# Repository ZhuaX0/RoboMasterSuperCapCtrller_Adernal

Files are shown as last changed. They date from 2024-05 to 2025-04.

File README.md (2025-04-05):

# <center>NOMAD的超级电容模组开源

项目负责人：
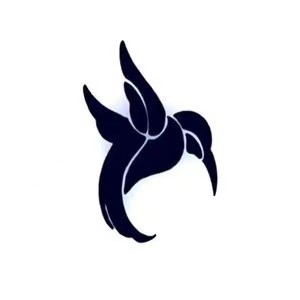
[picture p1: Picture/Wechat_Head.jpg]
Wechat_Head

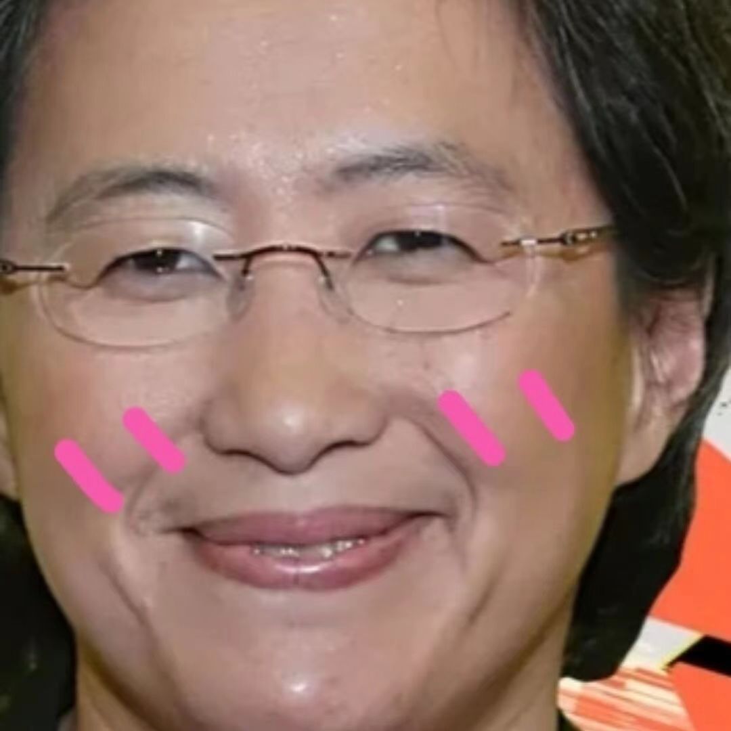
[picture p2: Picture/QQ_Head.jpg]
QQ_Head

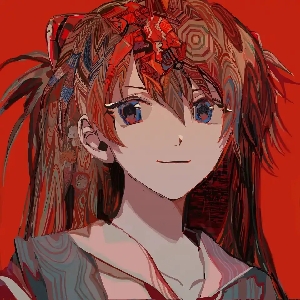
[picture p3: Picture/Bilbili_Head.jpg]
Bilbili_Head

(没错都是我)

## <center>前言
本开源文档于2024.5.5开始撰写，提笔于此，感慨万千。笔者于大一上学期入队，自大一暑假接手超电研发任务，至落笔此开源文档已有三个年头。这四年见证了队伍从联盟赛队伍一跃成为超级对抗赛的常驻队伍，笔者的技术、心态也逐渐成熟。依旧记得22赛季的赛场上，训练赛与小组赛受到单方面的薄纱而导致0胜绩大败而归，彼时的沮丧与不甘；依旧记得23赛季联盟赛，小组赛与某一线强队打平，万年弱队的滤镜被打破，彼时的兴奋与激动；依旧记得23赛季对抗赛，小组赛遇上两支国赛4强，对其实力与技术水平的由衷佩服。

笔者自接手超电研发任务以来，研发工作横跨22、23、24三个赛季。22赛季笔者技术水平不足，对队伍无实际贡献，因此22赛季的超电系购买淘宝某某创新的超级电容控制器与超级电容组使用；23赛季笔者借鉴中南大学FYT战队于CSDN的开源，研制一套可切换功率路径的串联降压方案，将其应用于赛场，并进行并联式双向四开关方案的预研；24赛季笔者对于并联式双向四开关的研制工作已经结束，并计划将其投入赛场。

本开源内容即笔者研制的并联式双向四开关方案的具体实现。纯属处于笔者的喜好，喜欢对自己的每个有代表意义的作品命名，该项目的超级电容控制器被命名为“Adernal”。**本开源项目不属于战队开源，属于个人开源**。本开源作为笔者的首次开源，将受到持续不定时的维护。由于笔者技术水平与精力有限，文档内的表述难免出现不恰当或者错误的表述(赛博口糊与赛博嘴瓢)，望各位谅解并欢迎指出。

## <center>控制器硬件设计
**该项目的物料选型请以BOM表为准，原理图中的物料仅供参考（仅仅封装与BOM表内物料是一样的）。**  
完整的硬件设计请参考PCB项目工程文件，本文档仅对项目中的关键硬件设计进行解释。
### 方案选择
笔者的研发工作进行过程中，RoboMaster高校系列赛的赛场上的超级电容控制器方案已近成熟。高校战队自行研制的超级电容控制器的硬件方案大致可划分为以下三种：

- 串联式降压/升压方案

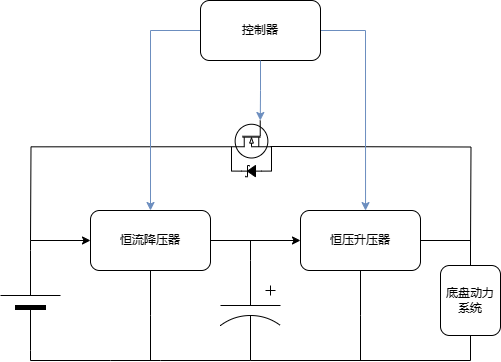
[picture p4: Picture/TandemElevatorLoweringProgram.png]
TandemElevatorLoweringProgram


该方案被认为是出现在RoboMaster高校系列赛赛场上最古早的硬件方案。来源于裁判系统电源管理模块Chassis电源接口的电流经过恒流降压部分为超级电容组恒功率（等于裁判系统功率限制）充电。电容组（可能有恒流降压输出）的能量经过一升压部分传递给底盘动力系统。此外，存在一电子开关将裁判系统Chassis电源与底盘动力系统直接连接，当电容组电压足够低导致升压部分无法正常工作时将升压部分失能同时导通电子开关。

笔者认为该方案的优点为搭建难度低，可通过选购适合的淘宝成品模块即可搭建一个可实现基本功能的硬件平台；控制难度低，控制器仅需控制恒流降压部分的使能与充电电流、升压部分的使能、电子开关的使能即可实现基本功能。该方案的缺点为硬件平台的体积过大，即便将所有硬件功能部分集成于单板、叠板，其体积对于结构组而言也是难以接受的；此外，在电容组电压较低的工况下，由于恒流降压部分与升压部分其输入、输出两端的压差较大，因此导致两者效率降低，从而导致该方案整体的能量转化效率较低，该方案在早期的RoboMaster高校系列赛受到普遍使用的原因为当时电容组的最高能量不受限制。

- 并联式四开关方案

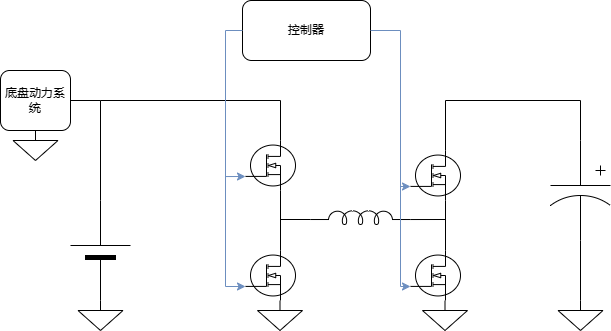
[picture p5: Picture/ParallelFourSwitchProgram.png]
ParallelFourSwitchProgram


该方案被普遍认为是当前RoboMaster高校系列赛赛场上的“版本答案”。将裁判系统Chassis电源串联一个ORing（这是可以省去的）后与底盘动力系统连接，将FSBB（Four-Switch-BuckBoost）与底盘动力系统所处网络并联，并将FSBB另一端与超级电容组连接。当底盘动力系统消耗功率低于裁判系统限制，FSBB将为超级电容组恒功率充电以保证裁判系统Chassis电源的输出功率与裁判系统功率限制保持一致；当底盘动力系统消耗功率高于裁判系统限制，FSBB将通过超级电容组的恒功率放电以保证裁判系统Chassis电源的输出功率与裁判系统功率限制保持一致。

笔者认为该方案的优点为：从功率、效率方面看，该方案性能足够高，是所有主流方案中最靠近规则限制下超级电容控制器理论最优性能的方案。该方案的缺点为：研发难度较高，存在微控制器编程与电子电路设计两大难点，并且在实际开发中，这两个难点具有较高的耦合，这要求研发者对电子电路设计与微控制器编程都具有一定的造诣（从另一个角度看可以算是优点，对这个方案的超电进行独立研发确实很锻炼人）。笔者当初想挑战自我，故将超级电容控制器的硬件方案定为该方案。

- 并联式两开关方案

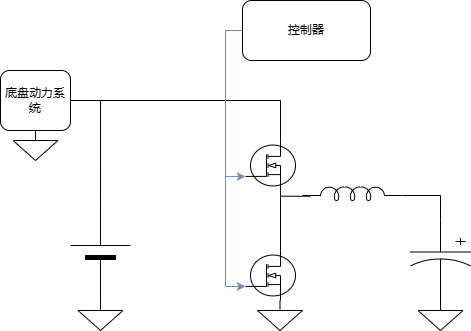
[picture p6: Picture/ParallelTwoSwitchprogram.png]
ParallelTwoSwitchprogram


该方案被认为是并联四四开关方案的简化版本。将裁判系统Chassis电源串联一个ORing（这是可以省去的）后与底盘动力系统连接，将单半桥变换器与底盘动力系统所处网络并联，并将单半桥变换器另一端与超级电容组连接。当底盘动力系统消耗功率低于裁判系统限制，单半桥变换器将为超级电容组恒功率充电以保证裁判系统Chassis电源的输出功率与裁判系统功率限制保持一致；当底盘动力系统消耗功率高于裁判系统限制，单半桥变换器将通过超级电容组的恒功率放电以保证裁判系统Chassis电源的输出功率与裁判系统功率限制保持一致。

笔者认为该方案的优点为搭建复杂度低于并联式四开关方案，相对于并联式四开关，从硬件角度看，该方案仅需要对一组半桥进行控制，从软件角度看，该方案无需考虑电容组电压处于电池电压附近时的控制问题；此外，该方案从理论上具有高于四开关的能量效率。该方案的缺点为：性能上限没有并联式四开关方案高；此外额外需要解决机器人死亡后底盘断电，电容组电压从半桥上管体二极管窜入母线导致“僵尸车”的问题。

### 关键物料选型
对于FSBB上的无源器件，笔者选型如下：

|物料类型|型号|
|:-----:|:--:|
|  C  |ZE11000UF35V119EC0014|
| L |BCIHP2213-150M|

其中，ZE11000UF35V119EC0014为容值为1000uF，20℃、100kHz下的ESR不高于8mR的高性能固态电容器；BCIHP2213-150M为感值为15uH，DCR典型值为5.62mR，额定电流为23.5A的一体成型功率电感。根据上述选型可以了解到电感纹波电流最高约为2.5A，输入/输出纹波电压最高不超过105.625mV。

对于半桥及驱动，笔者选型如下：
|物料类型|物料|
|:-----:|:--:|
|  MOS  |STL130N6F7|
|Driver |2EDF7275KXUMA1|

其中，STL130N6F7为Qg为42nC，Rds(ON)典型值为3mR的高性能N型开关管，具有不错的直流导通性能与开关性能；2EDF7275KXUMA1为灌电流8A，拉电流4A的隔离栅极驱动器，可以提供稳定的ns级的上升/下降时间。

>就目前行情来看，笔者更加推荐使用CSD18540作为开关管使用，该开关管虽然从正规渠道购买难度较大且价格高昂，但是淘宝部分商家售卖的这个管子报价为0.3RMB一颗，笔者听说该渠道的这个管子良品率高达70%(截止于2024上半年的消息)，且CSD18540的直流性能与开关性能都强于STL130N6F7。

对于模拟信号检测，笔者选型如下：

|物料类型|物料|
|:-----:|:--:|
|Sensor1|INA197AIDBVT|
|Sensor2|INA240A1DR|
|Opamp|COS722SR|
|Reference|CJ431|

其中，INA197AIDBVT为共模电压高达80V，放大倍数为50，带宽为300kHz的单向检测电流感应放大器，被放置于高侧检测母线电流；INA240A1DR为共模电压高达80V，放大倍数为20，带宽为400kHz，内置PWM抑制的双向检测电流感应放大器，被放置于高侧检测DCDC两端电流；COS722SR为供电电压在2.1V-5.5V，压摆率为7.2V/us的轨到轨运算放大器，被用来检查母线与电容组的电压；CJ431为供电电压高达36V，低至200mR的动态输出阻抗的电压基准芯片。

>当前，INA197的价格可能是绝大部分队伍难以接受的，笔者也是趁着该芯片价格低廉时购买。笔者在该项目中将该芯片作为母线功率环路反馈的提供者。考虑到裁判系统仅以10Hz反馈Chassis功率，因此母线电流的电流感应放大器可以认为仅需保证具有足够高的共模电压以满足在RM赛事工况下不会对芯片造成损坏，从这个角度来看，国内外芯片厂具有更多性价比之选。笔者不建议通过低侧采样的方式检测母线电流，考虑到RM赛事中超级电容控制器与超级电容组之间存在裁判系统超级电容管理模块，该模块与裁判系统电源管理模块之间存在着4Pin通讯线的直接连接（包含GND），不排除电流从4PIN线直接回流至裁判系统电源管理模块的可能性，导致低侧采样出现失准。

>针对于FSBB两端的电流采样，笔者认识到PWM抑制功能的用处是有限的。在INA240的数据手册-典型应用中，INA240被放置在半桥的SW网络检测无刷电机三相线的电流或螺线管的电流，但是INA240不适合放置在超级电容控制器的SW网络。下图为INA240数据手册中展示PWM抑制能力的曲线图，考察可知发生共模电压阶跃后输出反馈的失准时间约为1us，以该项目超级电容控制器为例，开关频率为160kHz，上升沿失准与下降沿失准占据整个开关周期约32%，半桥占空比较大或较小可能导致INA240无法反馈准确的电流值。(还在用INA240的原因是懒得改了)笔者在此更推荐采用低侧电流检测方案并直接使用运放搭建采样电路，可以更好的降低成本并锻炼开发人员的模拟电路搭建调试能力。
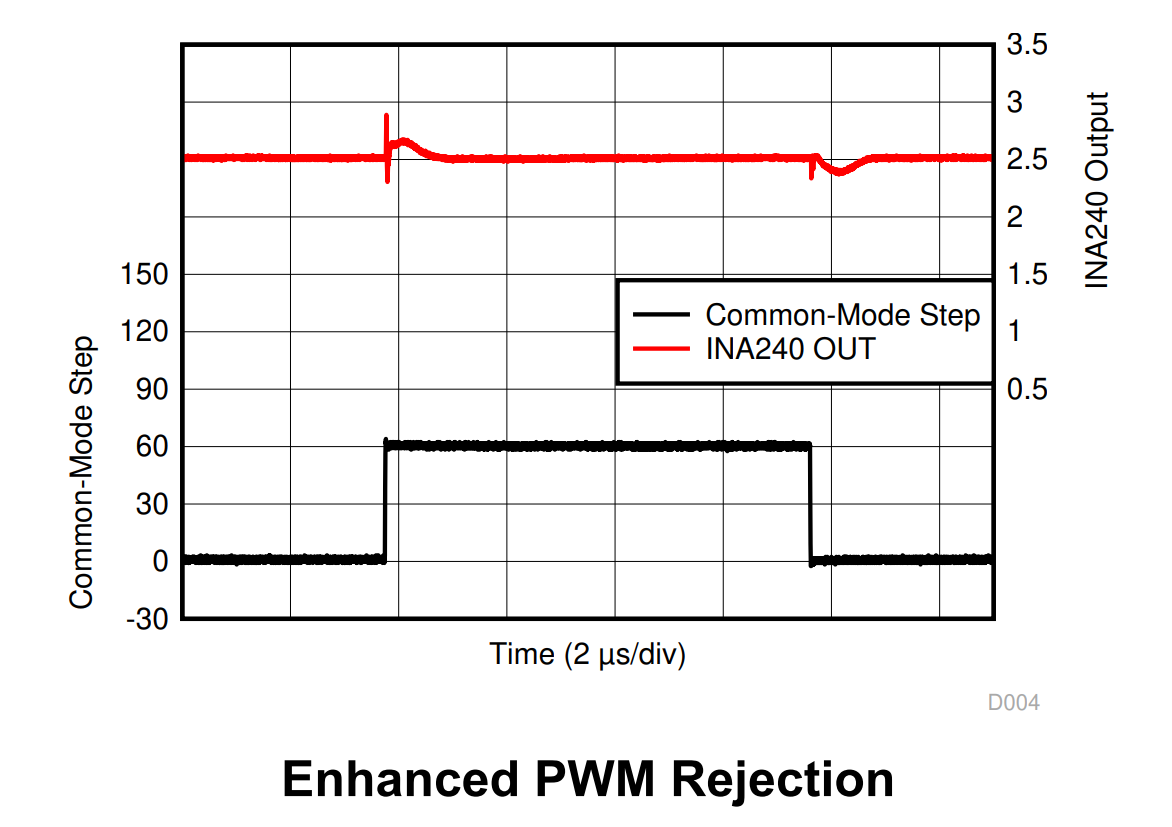
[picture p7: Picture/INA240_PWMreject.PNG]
INA240_PWMreject


在该项目中，以下杂散物料的选型也值得一谈：
|物料类型|物料|
|:-----:|:--:|
| C |CL21B473KBCNNNC|
|MicroControllerUnit|STM32G474CET6|

其中，CL21B473KBCNNNC为三星的容值47nF的MLCC，笔者在迭代过程中发现半桥SW噪声约为40-50MHz，该噪声耦合到整板的电压轨与信号网络导致超级电容控制器工作出现异常。笔者了解到该MLCC在30-70Mhz下具有30~50mR的阻抗（见下图）,在关键位置的电源轨铺设该MLCC，提高了整机工作的稳定性；STM32G474系意法半导体推出的主流微控制器，D-Power产品组合的一员，专门针对数字电源相关应用，例如D-SMPS、照明、焊接、太阳能系统逆变器及无线充电器。内置高分辨率定时器可提供高达184ps的分辨率，为电源提供精确电流、功率控制。

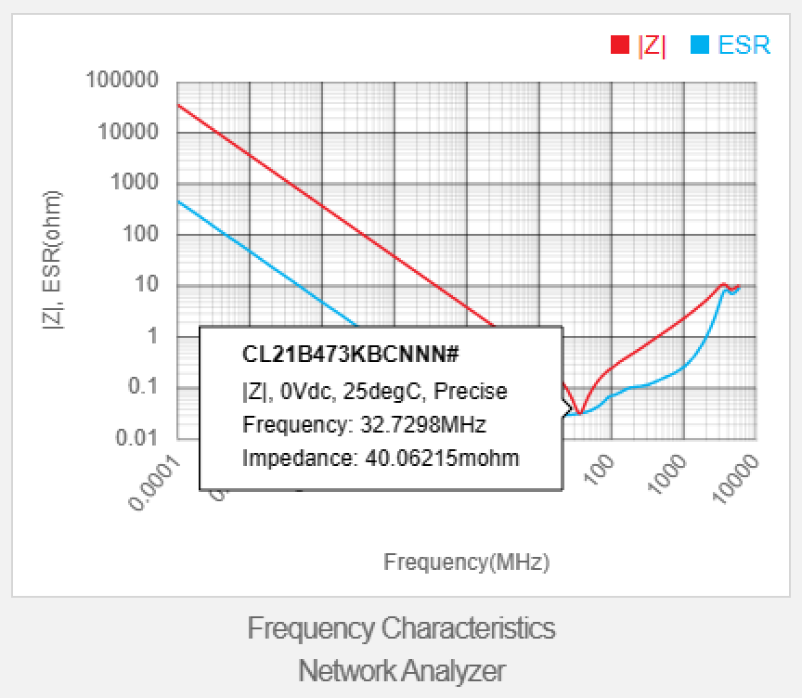
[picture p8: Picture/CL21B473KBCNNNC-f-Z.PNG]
CL21B473KBCNNNC-f-Z


### 关键电路设计
原理图中物料型号仅作为参考。

- 半桥驱动电路

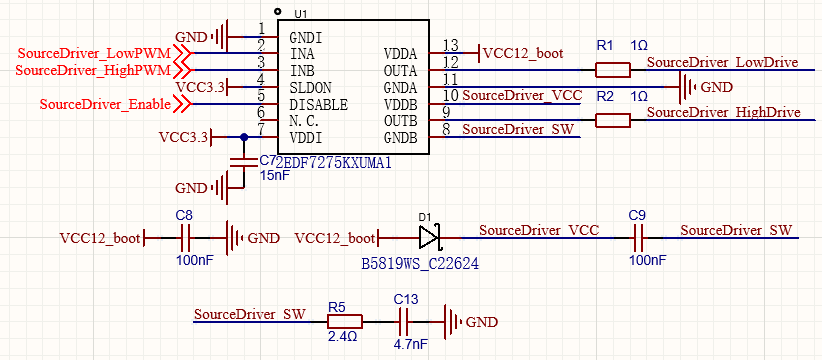
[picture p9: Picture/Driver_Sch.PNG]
Driver_Sch


对于半桥驱动器的控制部分，内置LDO未启用，电源轨直接使用数字信号的3V3电源；对于半桥驱动器的驱动部分，高侧N型开关管直接使用自举电路驱动，栅极驱动输出与开关管通过R1,R2电阻连接，用处是吸收Vgs振荡与减缓开关管的开启/关断时间以抑制电磁问题。R5、C13为RC组合，用于吸收半桥开关时SW网络的振荡能量，R、C值的敲定遵从[Analog Design Journal-Slyt740-Reducing noise on the output of a switching regulator](https://www.ti.com/lit/an/slyt740/slyt740.pdf?ts=1702068348410&ref_url=https%253A%252F%252Fwww.bing.com%252F)。
<br>
- 缓启动/防反接电路

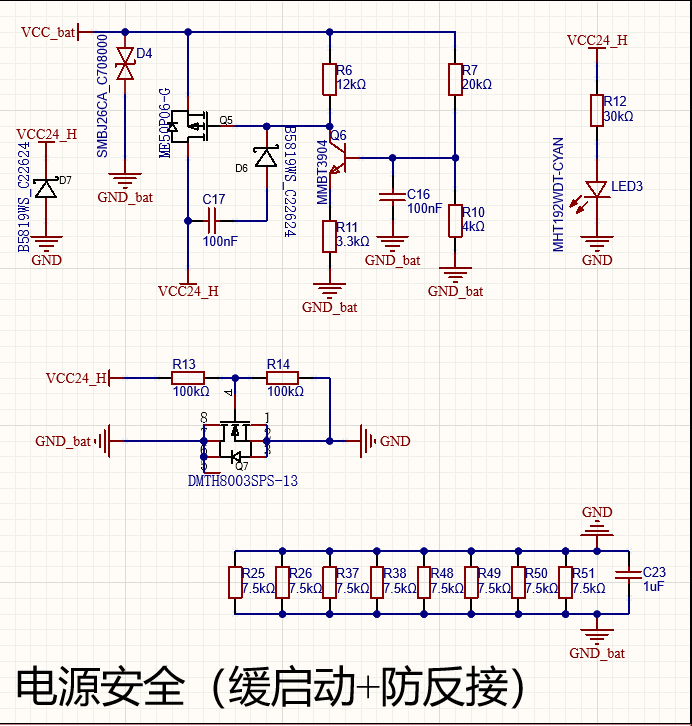
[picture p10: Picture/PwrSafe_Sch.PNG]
PwrSafe_Sch


电源硬件缓启动依托P型开关管的弥勒效应实现。当VCC_bat电压上升，VCC_bat通过R7、R10给C16充电，延长Q6(NPN-bjt)开启时间，Q6开启过程中，R6两端压差逐渐增大，Q5的Rds快速减小，当VCC24_H网络有0电压迅速上升至VCC_bat，经过C17与D6为P型开关管的栅极补充电荷，延长米勒平台。在Q5完全开启后，母线上任何电压尖峰的能量都由D4(TVS)消耗。  
防反接通过通过低侧N型开关管实现。当VCC24_H上升并保持稳定，经过R13、R14分压，Q7正常导通。当发生反接，GND_bat网络为电池电压，Vgs为0，Q7阻隔反向高压，实现防反接功能。考虑到未反接时，VCC24_H电压下降导致Q7挂断，此时GND为浮地，因此在GND与GND_bat间连接RC将GND网络下拉至GND_bat（别骂了笔者现在也觉得没啥用），反接时，电流从GND_bat经过该电阻与D7返回VCC_bat网络，板载芯片承受的负压仅为D7的正向偏置电压。
该电路提供Multisim仿真文件。
<br>
- 信号调理

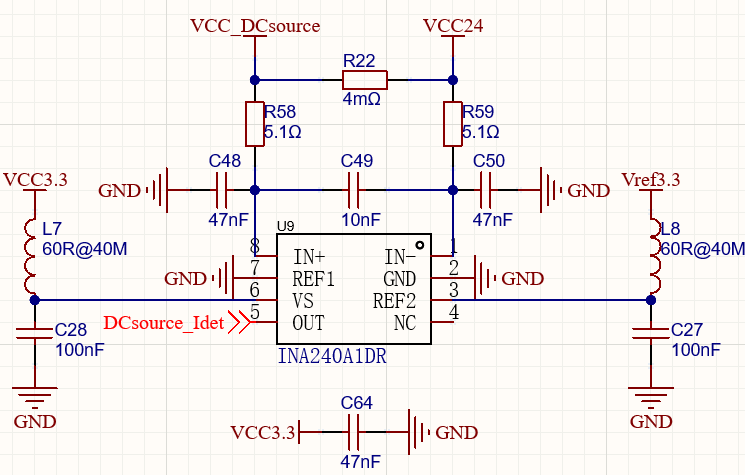
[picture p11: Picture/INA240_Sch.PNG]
INA240_Sch


以INA240的电流检测电路为例，检流电阻两端经过R58、R59、C48、C49、C50到达INA240的差分采样引脚。R58、C48与R59、C50这两个RC组合用于抑制半桥SW噪声耦合到电源轨上导致的共模瞬变，C48、C50需要连接至模拟信号参考层，C49用于差模滤波与抑制共模滤波器一致性偏差导致的差模误差。  
3V3电压基准经过L8（磁珠）与C27，经过INA240内部电阻分压为双向电流检测提供电压偏置。
>之所以为带有PWM抑制功能的INA240添加共模RC滤波器的原因在"关键物料选型"小节有所提及，下图截取与INA240的用户手册，对于5R的外部电阻，增益误差仅为0.17%，因此依旧能维持足够高水平的一致性。
>INA240_OutsideCommonModeFilter

### Layout

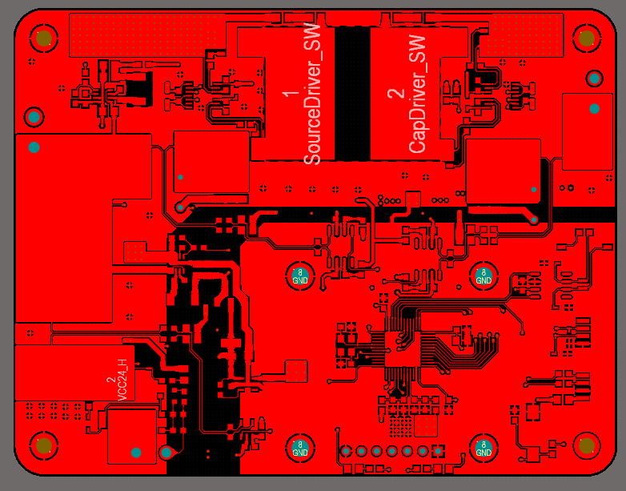
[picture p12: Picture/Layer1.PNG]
Layer1

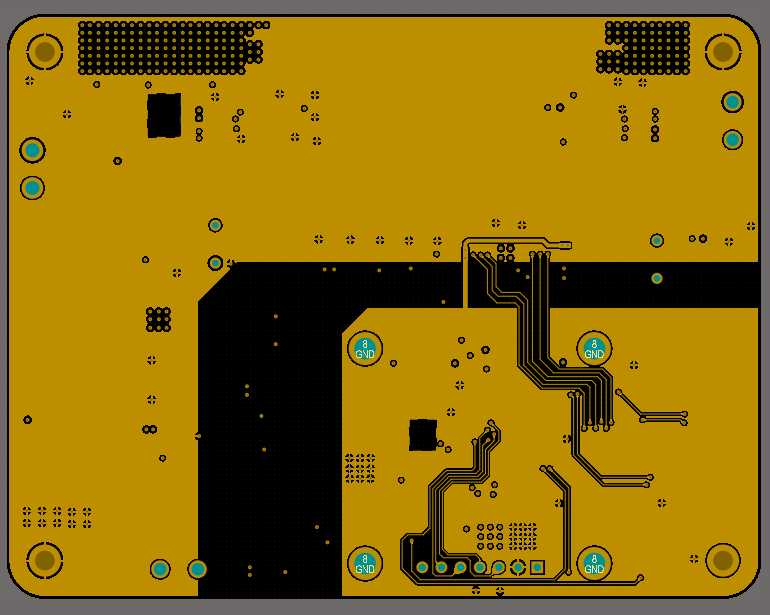
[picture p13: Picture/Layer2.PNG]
Layer2

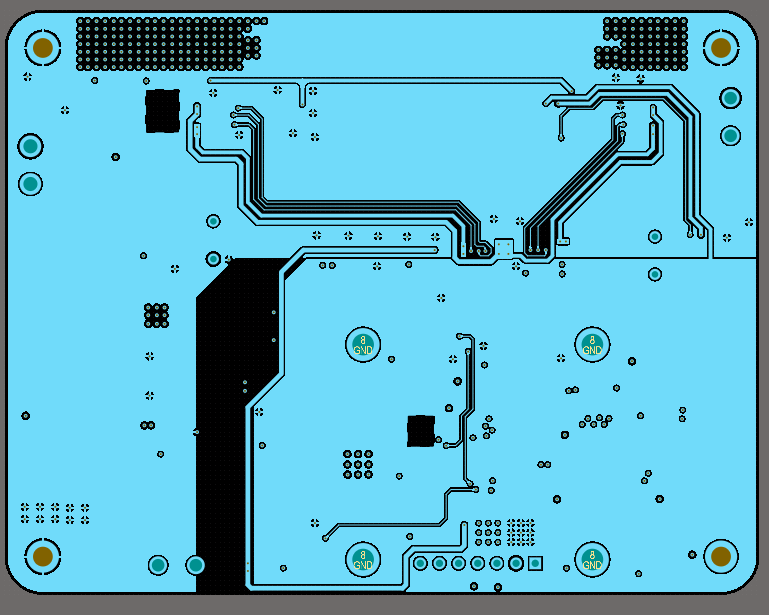
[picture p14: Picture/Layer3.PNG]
Layer3

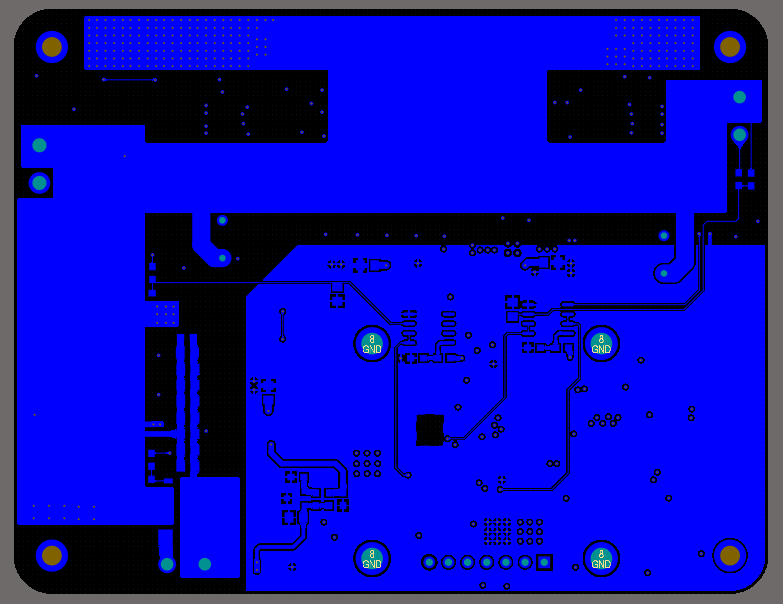
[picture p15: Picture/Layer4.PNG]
Layer4


在PCB板上，功率部分与控制部分被严格分隔，功率线通过区域填充增加宽度保证了足够的承载电流能力。功率区域中，1层铺地用于提高散热能力，2层铺地尽可能完整用以抑制杂散噪声并屏蔽其对下层信号的影响，三层铺地用于辅助散热。4层地为功率地，布置为“工字形”以保证FSBB工作过程中尽可能小的回路面积，以减小对外的电磁干扰。  
在控制区域，大部分信号器件贴装于1层，1层铺铜为数字信号参考层；2层为数字信号电源层，3层为模拟信号电源层，4层为模拟信号参考层。功率与信号的参考层通过与降压路径相同路径的走线进行单点连接，数字、模拟信号电源轨通过放置在微控制器模拟电源引脚附近的集中放置的过孔进行单点连接。

### 整体效果
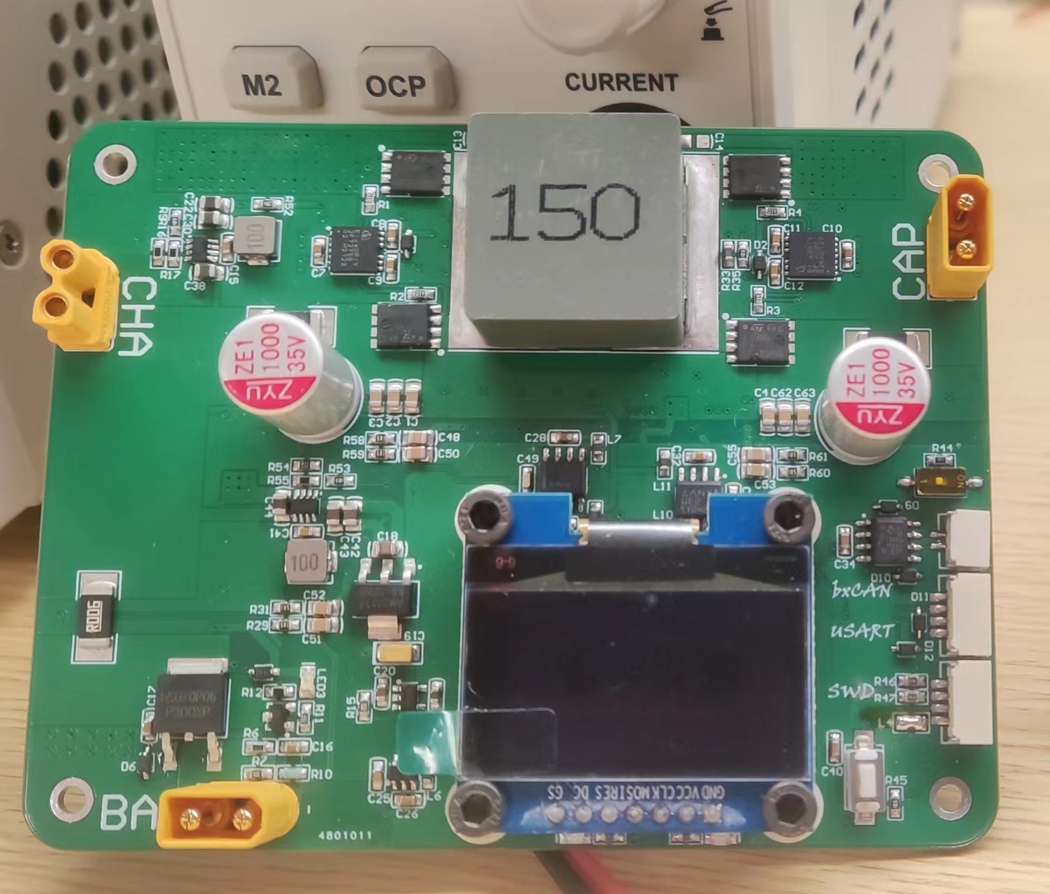
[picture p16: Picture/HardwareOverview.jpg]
HavdwareOverview


## <center>控制器软件设计
由于该项目中硬件与软件的耦合度较高，笔者对软件的开发伴随着硬件的研发工作持续了约1年的时间，不同部分的代码风格存在一定的变化。  
值得注意的是，由于控制方案的原因，本开源项目中提供的控制器软件设计并不能很好的发挥出控制器硬件的全部性能，详细的优化建议已在下文给出，根据优化建议对控制方案进行改进后，理论上将能发挥出控制器硬件的全部性能。  
STM32工程中，需要单独将LowOptZone.c与Safety.c文件的优化等级设置为-O0，以避免控制执行出现异常的现象。  
完整的硬件设计请参考STM32项目工程文件，本文档仅对项目中的关键软件设计进行解释。
### 环路控制
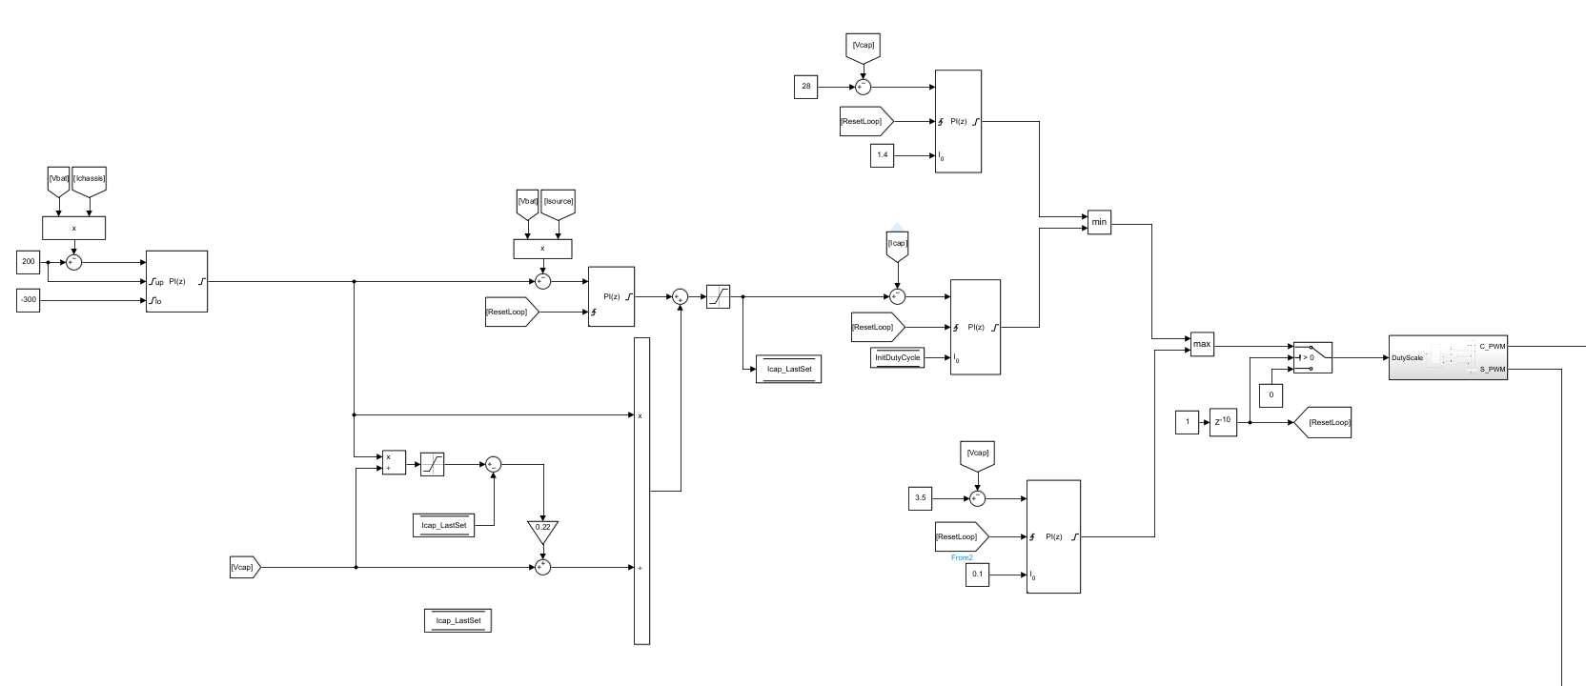
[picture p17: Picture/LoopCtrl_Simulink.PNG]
LoopCtrl_Simulink

环路控制方案的框图如上图所示。  
主环路为PID-FF-PID环路。最外层环路为母线（裁判系统Chassis电源输出）的功率PID环路，理想状态下，其期望恒定为裁判系统功率限制，反馈量为当前母线的实时功率，控制量为FSBB连接母线一端的期望功率（正负代表充电与放电）。

中间的FF环节将FSBB母线端期望功率( $P_s$ )转为电容组一端的期望电流( $I_c$ )。假定FSBB效率恒为100%（即 $P_s = P_c$ ， $P_c$ 为电容组当前充放电功率）， $I_c$ 与 $P_s$ 的关系可以通过下式直接表示：
$$I_c = \frac{P_c}{U_c} = \frac{P_s}{U_c}$$
该式被认为是简单模型，将上式引入控制环路后发现， $I_c$ 稳定后的收敛值准确，但是 $P_s$ 变化幅度较大时， $I_c$ 值出现抖动收敛的现象，其曲线类似于带阻尼的谐波曲线。  
推测上述现象是电容组的ESR导致， $P_s$ 变化后， $I_c$ 依上式发生变化，由于电容组存在ESR， $I_c$ 变化往往会导致 $U_c$ 短时间发生较大变化，因而下一次环路控制根据变化后的 $U_c$ 对 $I_c$ 进行调整。上述过程反复进行，其结果就是 $I_c$ 抖动并逐渐收敛至恒定值。解决抖动问题的方法就是将在控制模型中考虑电容组的ESR。修改简单模型为：
$$I_c = \frac{P_s}{U_c - I_{Clast}·ESR + I_c·ESR}$$
其中， $I_{Clast}$ 为上一次环路控制中FF输出的电容组电流期望值，整理得：
$$I_c = \frac{P_s}{U_c + ESR·(I_c - I_{Clast})}$$
上式被称之为ESR模型。欲求出 $I_c$ 的解析解，需要通过求根公式对二元一次方程进行求解，求出的解析解形式复杂，对微控制器运算压力较大，因此需要对上式进行简化以描述 $P_s$ 转成 $I_c$ 的过程。  
将简单模型 $I_c = \frac{P_s}{U_c}$ 引入上式中等号右边分母的 $I_c$ ，将上式简化为：
$$I_c = \frac{P_s}{U_c + ESR·(\frac{P_s}{U_c} - I_{Clast})}$$
上式被称之为简化后的ESR模型。将上式引入控制环路， $I_c$ 抖动问题得到了很好的解决，实际的 $P_s$ 可以在足够短的时间内达到预设的期望值，拥有远优于PID控制器的响应速度。但由于简化后的ESR模型不能很好的描述FSBB与电容组实际的表现，在电容组电压过低时， $P_s$ 的变化会为 $I_c$ 的曲线带来一定程度的“超调”（当然还是会收敛），在模型输入端添加数字滤波器可以很好的解决“超调”问题。理论上 $P_s$ 反馈与预设期望之间的误差与FSBB效率有很强的关联性，在本开源项目中提供的硬件平台下，若预设期望为205W，反馈值约为203W左右。

FF环节的输出作为最内环的期望值，最内环为电容组电流PID环路(正负代表电荷流动方向)，其反馈量为当前电容组的实时电流，控制量为广义占空比。

>简化后的ESR模型应用于环路控制过程中，需要对代入ESR模型的简单模型进行限幅，FF输出的电容组电流期望值也需要进行限幅，两者的限幅理应相同

>以下讨论未经实际测试（纯口嗨），请读者自行判断可行性。  
>ESR模型的表达式从形式上被认为适合使用数值迭代法得到更为精确的结果，其迭代方式类似于递归。根据ESR模型的表达式构造函数：
>$$f(x)=I_c = \frac{P_s}{U_c + ESR·(x - I_{Clast})}$$
>设定初始值 $x=\frac{P_s}{U_c}$ ，迭代一次的结果为：
>$$f(\frac{P_s}{U_c}) = \frac{P_s}{U_c + ESR·(\frac{P_s}{U_c} - I_{Clast})}$$
>上述结果与简化后的ESR模型具有相同的表达式。迭代两次的简要表达如下：
>$$f[f(\frac{P_s}{U_c})]$$
>以此类推，通过有限次的迭代，可使得计算结果与 $I_C$ 的理想期望值之间的误差小于任意的大于零的实数特定值，这种数值迭代的算法从理论上可以很好的解决电容组电压过低导致的输出失准，且不会带来部署滤波器导致时滞的问题。算法的运算时间与迭代次数近似呈正比，过多的迭代次数会对CPU带来一定程度的压力。

分析FSBB电路可以得到以下结论：
$$\frac{U_1}{U_2} = \frac{D_2}{D_1}$$
其中， $U_1$ 、 $U_2$ 分别为FSBB的1、2两端的电压值， $D_1$ 、 $D_2$ 分别为FSBB的1、2两边半桥上管PWM的duty。  
定义一 $\alpha$ 值，使其满足以下关系：
$$\alpha = \frac{U_1}{U_2} = \frac{D_2}{D_1}$$
定义FSBB的2端与母线连接（与底盘动力系统的电源轨并联），1端与电容组连接， $U_2$ 被认为是相对恒定的，因此可以得出在理想状态下 $U_1$ 与 $\alpha$ 呈正比的结论；与此同时， $\alpha$ 可以直接拆分成 $D_1$ 与 $D_2$ 。根据 $\alpha$ 的上述特性，笔者认为 $\alpha$ 很适合作为主环路的控制量， $\alpha$ 被定义为广义占空比。环路输出广义占空比后，被拆分成两边半桥的duty并更新半桥的占空比，这种控制方案被认为是解决电容组电压在电池电压附近导致存在振荡现象的有效手段。  
在实际进行的超电控制过程中，每次对FSBB提供PWM前都被建议为主环路的电容组电流环路预载积分值，预载积分值具体大小为： $\frac{U_c}{U_b}$ 。其中， $U_c$ 为当前电容组电压值， $U_b$ 为当前母线电压值，这种做法可以很好的解决FSBB于初始阶段存在短时大电流的问题。

主环路将与高电压环与低电压环竞争，高电压环与低电压环的反馈量都为电容组电压，控制量都为广义占空比。高电压环的期望为电容组的最高电压，低电压环期望为电容组的最低电压。在微控制器输出PWM前，两者都被建议预载积分值，高电压环的预载值为其积分限幅的上限，低电压环的预载值为其积分限幅的下限。

取主环路、高电压环、低电压环三者广义占空比输出的中位数，中位数对应的环路被认为竞争成功，拆分为实际占空比更新半桥duty。

>实际上，上述控制方案仍存在一定问题。若高电压环竞争成功而主环路竞争失败，主环路的所有PID环节的积分值将会持续增至积分限幅，若欲重新令主环路竞争成功，需要消耗一定的时间使积分值下降，直到主环路输出低于高电压环输出，低电压环与主环路的竞争同理，上述过程导致FSBB在特定状况下具有极慢的响应。笔者认为存在更优控制方案。需要注意的是以下对更优控制方案的讨论未经实际测试（纯口嗨），请读者自行判断可行性。
>考虑到RoboMaster高校系列赛中，裁判系统会以10Hz的频率通过串口向主控提供缓冲能量值，笔者认为可以将主环路的功率PID环替代为对缓冲能量的FF控制。定义30J为FF控制的期望值， $E_0$ 为微控制器获取到当前裁判系统反馈的缓冲能量， $E_1$ 为上一次裁判系统反馈的缓冲能量。欲保证下一次裁判系统反馈的缓冲能量为30J（维持在期望）,可以将FF控制的输出（FSBB连接母线一端的期望功率）更新为：
>$$P_s = \frac{2·E_0 - E_1 - 30J}{100ms} + P_{slast}$$
>其中， $P_{slast}$ 为上一次环路控制过程中该FF环节的输出。该式的推导不再赘述。
>笔者意识到功率环为主环路最外环的控制方案存在问题却依旧采用，原因是笔者原所处战队的历史遗留问题，战队原来很长一段时间根据缓冲能量剩余值为底盘动力系统的转矩电流乘以适当比例以实现功率控制，笔者对缓冲能量的控制在当时是不被接受的；其次，笔者对控制方案进行Simulink仿真过程中，仿真结果未出现该问题（不知道是什么原因）；最后一点是笔者没精力改了()

为了保证FSBB的效率尽可能高，对广义占空比拆分为半桥实际占空比的规则提出要求： $U_c$ 小于 $U_b$ 时，与电容组电源轨网络连接的半桥占空比为最高值； $U_c$ 大于 $U_b$ 时，与母线电源轨网络连接的半桥占空比为最高值；两边半桥上管同时开启的模态持续时间尽可能长。

环路控制方案提供Simulink仿真文件。考虑到不同版本Matlab对于打开Simulink仿真文件的一些妙妙特性，特此告知笔者通过R2022a版本的Matlab创建该".slx"文件，适配其余版本Matlab的".slx"文件恕笔者不再提供。

### 功能实现

- AlarmSystem

依托定时器上溢中断实现，同时提供多达32个非阻塞、非精确的以ms为单位的倒计时服务。该功能系项目初期实现，用于为超级电容控制器的工作任务提供时间片，对单次事件进行计时。
<br>
- Display  

更新板载OLED屏幕显示。反馈电容组电压、工作模式、安全信息等内容。
<br>
- LoopCtrl  

为FSBB提供10kHz的环路控制，FSBB的开关频率为160kHz。
<br>
- Mode  

设定三种控制FSBB的模式，分别为Silent、Work、Charge。各模式具体机制参阅《Adrenal用户手册》。FSBB的参数设定于此，最高充放电功率设定为200W，电容组一端最高充放电电流设定为13.5A。
<br>
- UsrMsg  

根据与机器人主控通过CAN帧通讯所遵守的协议，对接收到的CAN帧解包，对欲发送的信息进行封包。
<br>
- Safety  

超级电容控制器对自身的安全检查。检查项目包括8类，每类检测项根据安全事件的严重程度分为5个等级。安全管理的具体机制参阅《Adrenal用户手册》。

## <center>电容组设计

笔者认为，在RoboMaster高效系列赛的工况下，对于并联式四开关方案的控制器而言，超级电容组遵循以下以下设计规则将会得到最高的性能。

1. 超级电容组充满时，其两端电压值为30V。
2. 超级电容组充满时，其存储能量值为2kj。
3. 超级电容组的ESR需保证尽可能小。

根据以上设计规则，笔者将型号为WTR3V050F0Z-1840L的物料作为电容单体，将其按照11s1p的连接方式进行连接。  
WTR3V050F0Z-1840L为容值为50F，耐压为3V，ESR为22mR，额定电流为12A的超级电容单体。其组成的超级电容组容值为4.54F，耐压为33V，ESR为242mR。
当该超级电容组充满至30V时，其存储能量为：
$$E = \frac{1}{2}·C·U^2 = 2045.45J$$

电容组的均衡电路依托BW6103芯片实现。BW6103为是一款超级电容充电保护芯片，它内置高精度基准，确保输出精度达到±1%。内置的功率管使得过充保护后的泄流能力达到 0.2A@(VIN=2.95V)，很好地满足了超级电容级联使用时的充电特性。

考虑到200mA的泄放电流对于RoboMaster高校系列赛工况而言存在泄放能力不足的情况，考虑使用外置N型开关管AO3400A串联电阻作为主要泄放回路，BW6103此时仅用于泄放回路的触发。

提供超级电容组的PCB工程文件。

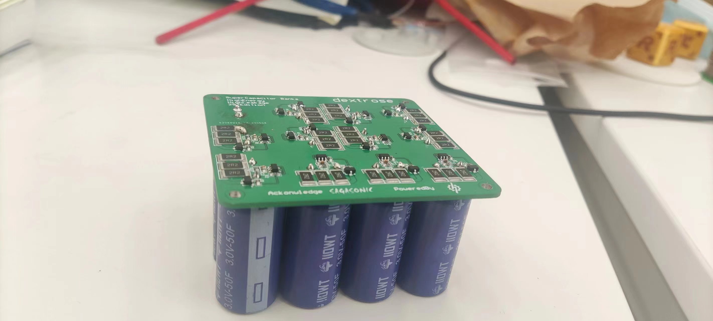
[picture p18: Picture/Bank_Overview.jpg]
Bank_Overview


## <center>实际表现

[麦轮原地陀螺](https://www.bilibili.com/video/BV1j6TweaEU2/?vd_source=5b2eb473ca9053cf0f2716bc338a787a)

## <center>后记
<!-- 感谢开源，感谢群友，感谢支持陪伴的人-->
落笔于此。笔者回想起大一入队，大二大三持续在队内干活的场景，那时候就想着，大学时光为这个比赛付出了这么多，总想留下一些什么东西不至于被忘记，故将这套超级电容控制器整理后开源。当各位看到这个文档的时候，笔者就摘下了RMer这个称号，笔者回顾自己的的RM个人生涯，倍感五味杂陈，内心再有万般不舍，也知道自己该走了，给更年轻的人腾位置，前方也有新的位置等着我。

感谢环节（不分先后）：  
感谢马斯克开源(不是  
感谢原大连理工大学凌bug战队的“光速翼”石澄今同学首次开源的《基于STM32G474的双向超级电容控制器》，笔者首次看其开源大受震撼，为笔者的开源项目的硬件方案奠定了基础。  
感谢原深圳大学RoboPilot战队的林子杰同学开源的《基于STM32F334的超级电容控制器》，其开源中的部分Layout思路解决了笔者画板时候的困惑，与其交流也收获颇丰。  
感谢西交利物浦大学GMaster战队的超级电容控制器开源，其开源中的数字滤波方案被笔者在本开源中很好的沿用。  
感谢原河北工业大学山海Mas战队的“Sirius-RX”同学，笔者时常与该同学交流超级电容控制器的研发心得，虽然其本人也独立开源研发成果且具有足够高的质量但是好像没发到RMbbs上面，因此似乎没什么人气，欢迎前去[围观](https://github.com/Sirius-RX/SP_Ultra_CAP/tree/main)。  
感谢香港科技大学ENTERPRIZE战队开源的《数控超级电容方案开源》，其开源中详细的安全处理部分很好的启发笔者。  
感谢广州城市理工学院野狼队的“空格”同学，请我吃了寿司和薯条，为我的研发工作提供能量（物理上的）。  
也感谢RM硬件交流群（826872833）的各位活跃群友，在笔者研发过程中，经常在群里问各种问题，吃百家饭。笔者有今天的技术水平与研发结果离不开各位群友的慷慨喂饭。  

## 补充

### 授权1

兹授权“深圳斯特埃科技有限责任公司”使用本开源项目用以商业目的。

授权期限：  2025  年 4 月 5 日至  2026  年 4 月 5 日。

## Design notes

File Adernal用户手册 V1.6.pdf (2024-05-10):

# Adernal 超级电容控制器用户手册

此文档为用户手册，以尽可能简洁易懂的语言让使用者快速上手而编写

## 警告！严禁将人体皮肤或任何静电源接触在任何工作状

## 态下的超级电容控制器！

## 严禁将超级电容控制器置于任何高温热源附近！

## 超级电容控制器为高发热器件，使用时注意散热。

此超级电容控制器仅为 DEMO 版本，仅在实验室条件下稳定工作，不保证其在任何条件 下皆能稳定工作，特此告知。

版本 | 主要改动 1.0 -- 1.1 修改控制帧、反馈帧内容 1.2 修改初始化帧内容 1.3 ①完善“Work 模式”的表述。 ②完善“工作强度”的表述。 ③修改协议的 Exceed 部分。 ④修复反馈帧字节数错误问题。
| ⑤对电容组插接时电压提出要求。
1.4 | ①重构对“安全管理”的表述 ②添加 OLED 屏幕显示信息的释义
1.5 | ①完善对 ”Exceed ”的表述 ②修改对“工作强度”的表述
1.6 | 为 Exceed 功能添加注意事项

# 一、 装配

超级电容控制器提供 4 个适合 2.5 直径螺丝固定整板的通孔，可以将超级电容控制 器与任意刚体固连。具体尺寸见下图（高度约为 21）。

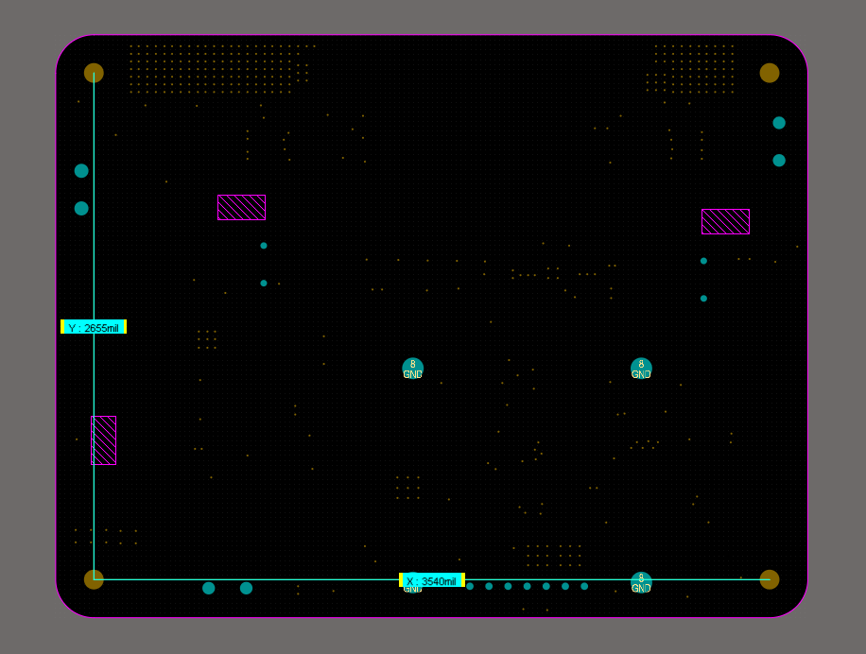
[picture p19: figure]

原则上，超级电容控制器的装配位置需要与高温热源（例如电源管理模块）及电磁 敏感装置（例如场地交互模块）保持尽可能远的距离。
若装配位置不可避免地需要靠近高温热源，需要对热源与超级电容控制器部署尽可 能完善的散热措施（包括且不限于贴装散热片、风扇主动散热），并且从软件上限制超 级电容控制器的 Pchassis 期望功率。压力测试过程中的热成像图如下： 压力测试过程中的热成像图如下：

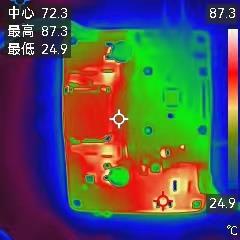
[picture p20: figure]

若装配位置不可避免的需要接近电磁敏感装置，并且在实际工况中已经对电磁敏感 装置的工作产生了一定的影响，可以要求硬件工程师在控制器上的 R5,R8 焊盘上贴装 0805 或更大尺寸的 2R4 电阻，在 C13,C14 焊盘上贴装 0805 或更大尺寸的 4.7nF 陶瓷 电容，需要注意陶瓷电容需要在 0~30V 的偏置下保持尽可能稳定的容值，这种举措可 能会导致一定程度上的板级发热。
超级电容控制器需要尽可能避免受到瞬时大冲量的冲击以免造成板载元件损坏。针 对于上述问题，一种可行的装配方案如下示意图。

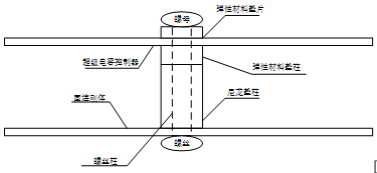
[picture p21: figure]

[图片]

上述方案中，超级电容控制器基板需要与机器人所处地面平行，图中，尼龙垫柱的 作用为避免控制器的电子元件与金属部分与所固连的刚体接触，弹性材料垫柱与弹性材 料垫片的作用为对超级电容控制器受到的瞬时大冲量进行缓冲，弹性材料可以使用 TPU 材料。

# 二、 连接

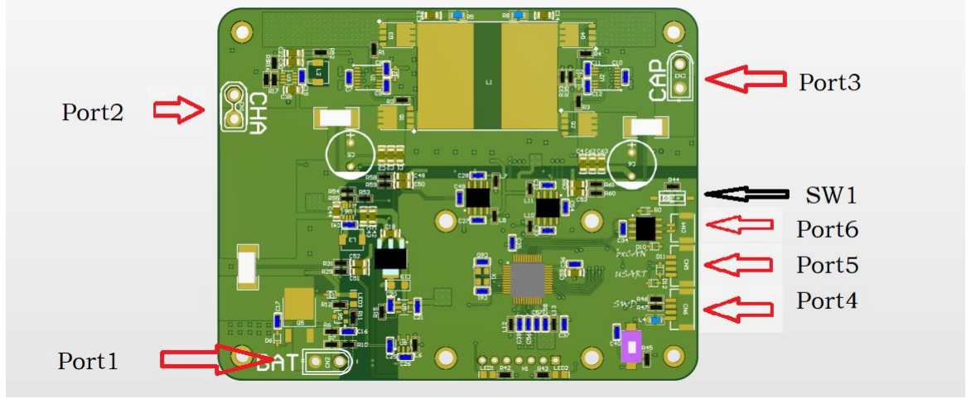
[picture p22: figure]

功率连接器 P1~P3 使用的是 Amass 的 XT30 连接器。
P1 为超级电容控制器的电源输入(BAT)，在 RoboMaster 应用中将其连接至电源管 理模块的 Chassis 端口。
P2 为超级电容控制器的输出端口(CHA)，在 RoboMaster 应用中将其连接至底盘动 力系统的供电。
P3 与超级电容组进行连接。将该连接器与超级电容组进行连接时需保证电容组电 压不高于 10V，以免发生打火现象。
信号连接器 P4~P6 使用的是日压端子(JST)的 GH1.25 连接器。
P4 为 4Pin 连接器，暂不考虑向用户开放。
P5 为 4Pin 连接器，暂不考虑向用户开放。
P6 为 2Pin 连接器，为 bxCAN 接口，用以与其余微控制器通讯，接受控制命令与 返回数据。
SW1 为 1Port 拨码开关，控制是否在总线两端连接 120R 电阻，决定超级电容控制 器是否为 CANbus 的终端设备。

# 三、 控制

在提供通讯协议前，有必要对超级电容控制器工作过程，及控制、返回数据所涉及 到的专有名词进行解释。

一、适配电容组类型
超级电容控制器提供三种类型的超级电容组适配，分别为类型 1、类型 2、类型 3。 不同类型仅在电容组最高充电电压有所区别，最低电压均为 3.5V。
类型 1：电容组最高充电电压为 24V。
类型 2：电容组最高充电电压为 28V。
类型 3：电容组最高充电电压为 30V。
Note1：在设置类型前用户需深刻了解与超级电容控制器连接的超级电容组允许在 什么类型下进行工作，超级电容控制器无自动检测能力，对此方面的避险能力有限。若 用户设置的类型超过了超级电容组的能量储存能力，最严重的情况是超级电容组与超级 电容控制器均发生不可逆损伤。
Note2：根据非官方消息，裁判系统电容管理模块上电流检测芯片检测端最大共模 电压仅为 28V，因此类型 3 在 RoboMaster 赛事应用中是存在风险的，但因为 30V 相对 于 28V 收益巨大并且部分战队反馈在比赛中电容组电压在 28V 至 30V 之间并未出现严 重损坏现象，故特意设置类型 3。

二、工作模式
超级电容控制器根据应用场景的不同，设置了三种工作模式，分别为Work，Charge， Silent。
超级电容控制器的简要拓扑如下：

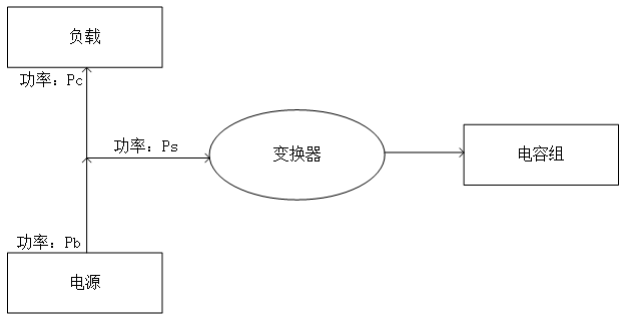
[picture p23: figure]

当能量流动方向与箭头方向一致时，对应的 P>0。
根据能量守恒定律，下式恒成立。
Pb = Pc + Ps | 1

在 Work 模式下，超级电容控制器尽可能保证Pb恒定于Pb_Set (Pb_Set由用户设置)。 即满足下式
Pb_Set = Pb = Pc + Ps | 2
因为超级电容控制器的工作能力有限，对上式作出如下限制：
① 超级电容组低压时不适合大功率充放电行为，因此在超级电容组低压时对充放 电行为采取限流措施。充电时，PbSet > Pb = Pc + Ps；放电时，PbSet < Pb =

Pc + Ps。
② 超级电容组达到电压限制边界时，变换器仅保证电容组电压恒定，分两种状况。 第一种，当变换器持续为超级电容组充电达到超级电容组最高电压时，变换器 保证超级电容组电压恒定拒绝为其充电，此时PbSet > Pb = Pc + Ps；第二种， 当变换器持续为超级电容组放电达到超级电容组最低电压时，变换器保证超级 电容组电压恒定拒绝为其放电，此时PbSet < Pb = Pc + Ps。
③ 超级电容控制器不能承受过大的放电功率，当放电需求过大时对超级电容组的 放电功率加以限制。此时PbSet < Pb = Pc + Ps。

为满足 RoboMaster 赛事应用中“攒一波”的需求，特意设置 Charge 模式。在 Charge 模式下，超级电容控制器尽可能保证：
{

Pbset = Pb = Pc + Ps
Ps > 0

3

因为超级电容控制器的工作能力有限，对上式作出如下限制：
① 超级电容组低压时不适合大功率充电行为，因此在超级电容组低压时对充电行 为采取限流措施。此时PbSet > Pb = Pc + Ps。
② 超级电容组达到电压限制边界时，变换器仅保证电容组电压恒定。当变换器持 续为超级电容组充电达到超级电容组最高电压时，变换器保证超级电容组电压 恒定拒绝为其充电，此时PbSet > Pb = Pc + Ps。

在 Silent 模式下，下式恒成立：
{

Pb = Pc
Ps = 0

4

控制器工作期间，当前所处模式在 OLED 屏幕上实时反馈：

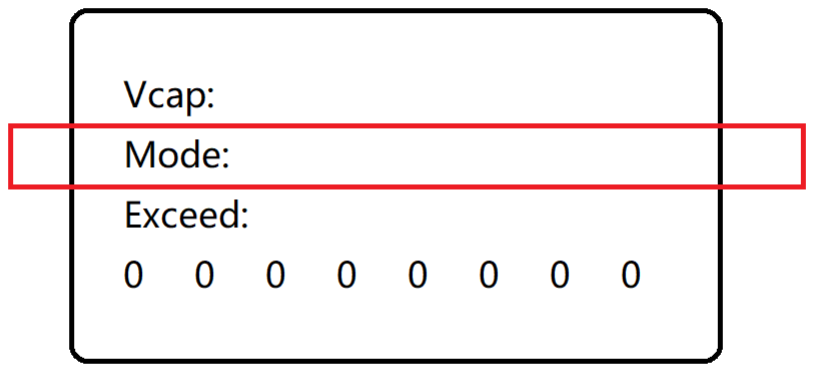
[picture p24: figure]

三、电容组电压
向主控返回的电容组电压经过了 ESR 修正，不能表示电容组当前的真实电压，但是 更能体现电容组当前剩余能量。建议主控接收到电容组电压之后进行如下处理：

μ =

Ucap

2 | − Umin
| 2

Umax

2 | − Umin
| 2

5

μ为当前电容组剩余能量的百分比，Ucap为当前电容组电压，Umax为电容组最高 电压限制，Umin为电容组最低电压限制。
控制器工作期间，电容组电压值在 OLED 屏幕上实时反馈：

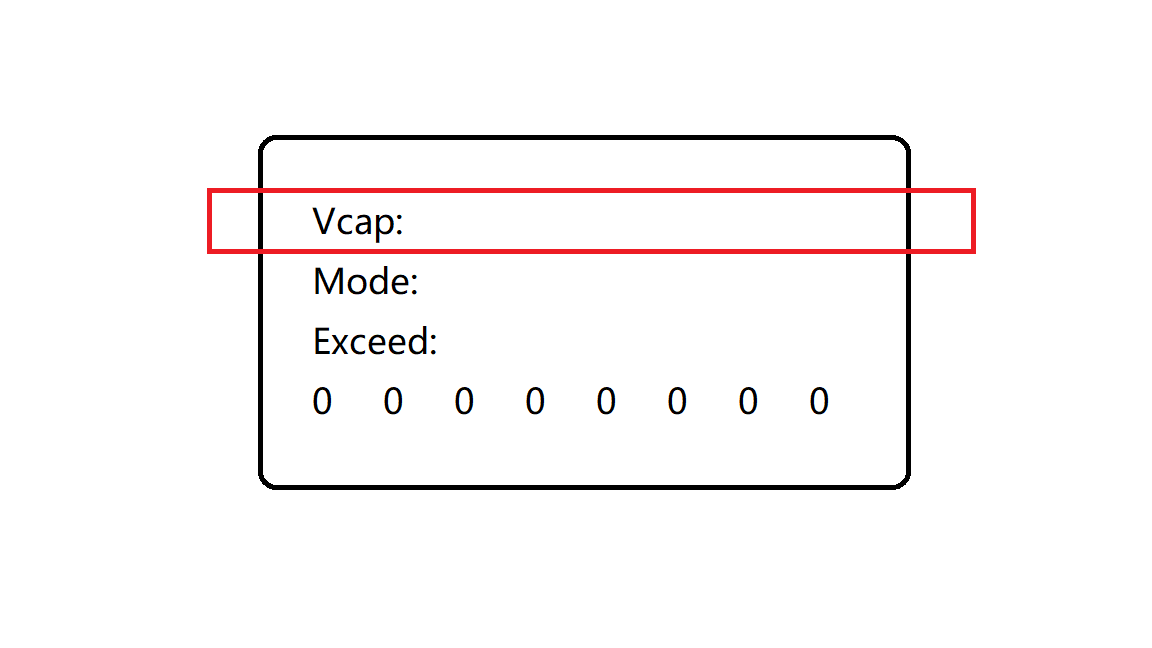
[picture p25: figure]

四、工作强度
在超级电容控制器工作过程中，存在最高充放电电流限制、最高放电功率限制，分 别对应着工作强度 1(α1)与工作强度 2（α2）。
两种工作强度为百分比值，可以用下式表示:

{

α1 = |
Icap

Icap_max|

α2 = |
Ps

Ps_max|

6

在 Exceed 处于 Off 时，α1与α2均无法超过 100%，在 Exceed 处于 On 时，α1将不 能超过 135%。

五、Exceed
超级电容控制器不论处于上述任何一种工作模式(work,silent,charge)中，其工作能 力不会超过各元器件数据手册提供的可持续额定值。考虑 RoboMaster 赛事工况中，绝 大部分队伍的超级电容控制器与电容组的工作常常超过手册的可持续额定值，为了在赛 场上保证较高性能与其他队伍对抗，推出 Exceed 模式。 超级电容控制器正常工作下的额定性能参数（电容组充放电电流、超级电容控制器 放电功率）往往受到超级电容组的制约，进入 Exceed 模式后，超级电容控制器不再考 虑超级电容组的寿命，将额定性能参数提高至超级电容控制器上器件的可持续额定参数。 其实际表现为，维持恒定 Ps 的能力上升 35%。
需要注意的是，虽然超级电容控制器不具备自行关闭 Exceed 的能力，但是长时间 处于 Exceed：On 下工作是不安全的行为。Exceed 被设计为仅在电容组低压下仍需要大 功率输出的解决方案。对于需要处于 Exceed：On 工作的超级电容控制器，散热片的贴 装是必不可少的；并且每次 Exceed 的持续时间不应超过 10 秒，结束一次 ExceedOn 之 后，需要保留足够的时间等待控制器与电容组温度降低后才能准备下一次 ExceedOn。 控制器工作期间，Exceed 开启与否在 OLED 屏幕上实时反馈：

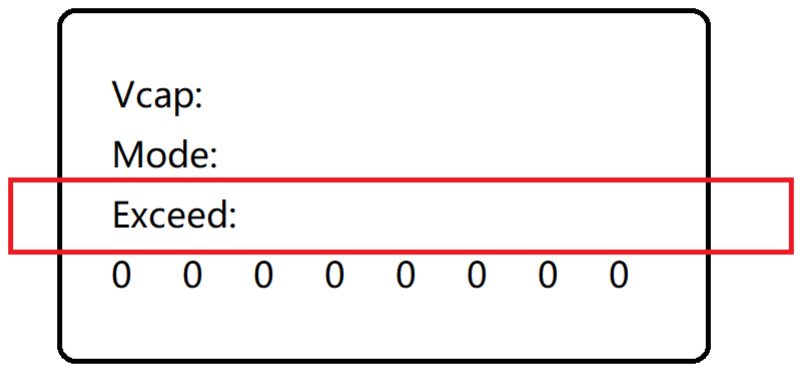
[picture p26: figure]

六、安全管理
超级电容控制器在任何工作状态时刻进行对自身的安全检查。 安全管理对检测项问题严重程度分为以下不同等级：
0：安全。
1：警告。达到该等级的检测项不干预正常业务的进行，但向主控反馈警告信息。 2：风险。达到该等级的检测项强制停止变换器工作，等检测项安全等级下降后允 许变换器工作。
3：危险。达到该等级的检测项强制停止变换器工作，按下 reset 键重置控制器以重 置该安全等级。
4：不可逆损伤。达到该等级的检测项强制停止变换器工作，需要硬件工程师勘误 后重置该安全等级。

安全管理存在以下检测项：
① 固件错误：该错误涉及的安全等级有：安全、警告、不可逆损伤；时刻检查。 用户侦测到该检测项达到不可逆损伤的安全等级，应立即将控制器交换与硬件 工程师并详细描述发生错误时控制器所处工况。
② CAN 错误：该错误涉及的安全等级有：安全、风险；时刻检查。用户侦测到该 检测项达到风险的安全等级，需检查主控的 bxCAN 协议是否正确，并检查信 号传输连接是否良好。
③ 过热保护：该错误涉及的安全等级有：安全、警告、风险、不可逆损伤；时刻 检查。用户侦测到该检测项达到风险、警告的安全等级，需要为控制器部署更 高水平的散热措施；若检测项达到不可逆损伤的安全等级，应立即将控制器交 换与硬件工程师并详细描述发生错误时控制器所处工况。
④ 校准错误：该错误设计的安全等级有：安全、危险；每次重置控制器后仅检查 一次。用户侦测到该检测项达到危险的安全等级，通过按下 Reset 按键或者重 新为控制器上电以尝试撤销该安全等级。若反复执行以上措施安全等级依然处 于危险，应立即将控制器交换与硬件工程师并详细描述发生错误时控制器所处 工况。
⑤ 电压错误：该错误涉及的安全等级有：安全、风险；时刻检查。用户侦测到该 检测项长时间处于风险的安全等级，应检查并保证电池电压处于 19.5V与 27.5V 之间，电容组电压处于 3.5V 与用户设定的电容组最高电压之间。若上述条件得 到保证且安全等级依旧为风险，应立即将控制器交换与硬件工程师并详细描述 发生错误时控制器所处工况。
⑥ 电流错误：该错误涉及的安全等级有：安全、警告、风险、不可逆损伤；时刻 检查。用户侦测到该检测项达到不可逆损伤的安全等级，应立即将控制器交换 与硬件工程师并详细描述发生错误时控制器所处工况。
⑦ 功率错误：该错误涉及的安全等级有：安全、警告、风险、不可逆损伤；时刻 检查。用户侦测到该检测项达到风险、不可逆损伤的安全等级，应立即将控制 器交换与硬件工程师并详细描述发生错误时控制器所处工况。
⑧ 采样错误：该错误涉及的安全等级有：安全、警告、危险；时刻检查。用户侦 测到该检测项达到危险的安全等级，应立即将控制器交换与硬件工程师并详细 描述发生错误时控制器所处工况。
控制器工作期间，各检测项的安全等级在 OLED 屏幕上实时反馈：

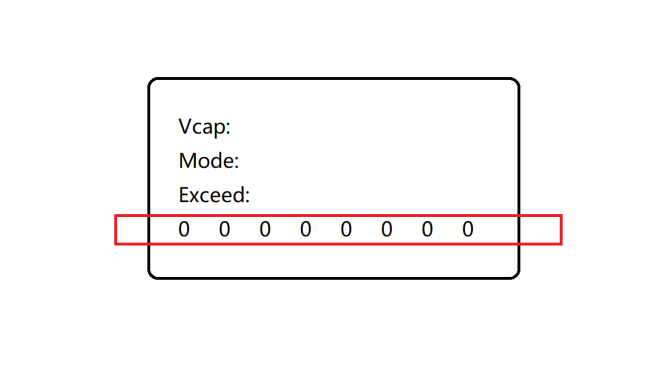
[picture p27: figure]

从左至右，各数字所代表的含义分别为：固件错误检测项的安全等级，CAN 错误检 测项的安全等级，过热保护检测项的安全等级，校准错误检测项的安全等级，电压 错误检测项的安全等级，电流错误检测项的安全等级，功率错误检测项的安全等级， 采样错误检测项的安全等级。

七、通讯协议
1.就绪帧（超电控制器 tx，主控 rx）
ID:0X005
标准数据帧，1byte(s)
位值偏移 | 释义
0~7 | 0xFF：控制器已就绪，可以进行 can 数据收发 0x00：控制器不可用，接受的所有 can 帧将被忽略

Tips：该帧会在控制器上电后发送一次，工作中因为安全等级的变化可能再次 进行发送。

2.初始化帧（超电控制器 rx，主控 tx）
ID:0X002
标准数据帧，1byte(s)
位值偏移 | 释义
0~7 | 0x00：超级电容组类型 1 0x01：超级电容组类型 2 0x02：超级电容组类型 3

Tips：该帧每次上电后仅接受一次。

3.反馈帧（超电控制器 tx，主控 rx）
ID:0X003
标准数据帧，6byte(s)
位值偏移 | 释义
0~7 | ESR 修正后的电容组电压高 8 位
8~15 | ESR 修正后的电容组电压低 8 位
16~23 | 工作强度 1
24~31 | 工作强度 2
32~39 | 电源输入功率高 8 位
40~47 | 电源输入功率低 8 位
Tips：电容组电压为真实电压值 X100 后忽略小数，例如电容组电压为 12.3421V，发送数据 1234。
工作强度为实际工作强度 X100 后忽略小数，例如当前工作强度 1(2)为 0.8147，发送数据 81。
电源输入功率为真实功率值 X100 后忽略小数，例如电容组电压为 12.3421W， 发送数据 1234。
每 500ms 传输一帧。

4.控制帧（超电控制器 rx，主控 tx）
ID:0X004
标准数据帧，3byte(s)
位值偏移 | 释义
0~7 | PbSet
8~15 | 0x00：Exceed 失能 0x01：Exceed 使能
16~23 | 0x00：Silent 工作模式 0x01：Work 工作模式 0x02：Charge 工作模式

Tips：用户可以仅在必要时传输该帧，避免相同内容反复发送影响控制器性 能。控制权限低于控制器内置安全管理逻辑

4.安全提示帧（超电控制器 tx，主控 rx）
ID:0X001
标准数据帧，8byte(s)
位值偏移 | 释义
0~7 | 固件错误检测项的安全等级
8~15 | CAN 错误检测项的安全等级
16~23 | 过热保护检测项的安全等级
24~31 | 校准错误检测项的安全等级
32~39 | 电压错误检测项的安全等级
40~47 | 电流错误检测项的安全等级
48~55 | 功率错误检测项的安全等级
56~63 | 采样错误检测项的安全等级
Tips：初始化时传输一次该帧，上述任意一个检测项安全等级变化时再次传输

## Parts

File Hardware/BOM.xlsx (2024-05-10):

 | Comment | Description | Designator | Footprint | Quantity
1 | 47nF | CL21B473KBCNNNC | C1, C2, C3, C4, C45, C47, C48, C50, C51, C52, C53, C55, C62, C63, C64, C65, C66 | C-RAD-0805 | 17
2 | ZE11000UF35V119EC0014 |  | C5, C6 | CAP-TH_BD10.0-P5.00-D0.6-FD-A | 2
3 | 15nF |  | C7, C10 | C-RAD-0603 | 2
4 | 100nF |  | C8, C9, C11, C12, C15, C16, C17, C24, C26, C27, C28, C29, C31, C32, C33, C34, C35, C36, C37, C39, C40, C41 | C-RAD-0603 | 22
5 | 4.7nF |  | C13, C14 | C-RAD-0805 | 2
6 | 10uF |  | C18, C46 | C-RAD-0805 | 2
7 | CA45-A-16V-10uF-K |  | C19 | CAP-3216 | 1
8 | 1uF |  | C20, C21, C23, C56, C58 | C-RAD-0603 | 5
9 | 22uF |  | C22, C30, C38, C42, C43, C44 | C-RAD-0805 | 6
10 | 2.2uF |  | C25 | C-RAD-0603 | 1
11 | 10nF |  | C49, C54, C57 | C-RAD-0603 | 3
12 | 4.7uF |  | C59 | C-RAD-0805 | 1
13 | 13pF |  | C60, C61 | C-RAD-0603 | 2
14 | XT30UPB-F |  | CN1 | CONN-TH_XT30UPB-F | 1
15 | XT30UPB-M |  | CN2, CN3 | CONN-TH_XT30UPB-M | 2
16 | A1257WR-S-2P |  | CN4 | CONN-SMD_A1257WR-S-2P | 1
17 | HC-1.25-4PWT |  | CN5, CN6 | CONN-SMD_4P-P1.25-HC-1.25-4PWT | 2
18 | B5819WS_C22624 |  | D1, D2, D6, D7 | SOD-323_L1.8-W1.3-LS2.5-BI | 4
19 | SMBJ26CA_C708000 |  | D4 | SMB_L4.6-W3.6-LS5.3-BI | 1
20 | UDD32C15L01 |  | D9, D10, D11, D12 | SOD-323_L1.8-W1.3-LS2.5-BI | 4
21 | MWSA0402S-100MT |  | L2, L3 | L-SMD-4.5 | 2
22 | L_600Ω@100MHZ |  | L4 | 0805-1 | 1
23 | 60R@40M |  | L5, L6, L7, L8, L9, L10, L11, L12, L13 | 0603-1 | 9
24 | MHT192WDT-CYAN |  | LED1, LED2, LED3 | LED_0805 | 3
25 | STL130N6F7 |  | Q1, Q2, Q3, Q4, Q7 | VDFN8 | 5
26 | HSU70P06 |  | Q5 | TO-252-2 | 1
27 | MMBT3904 |  | Q6 | SOT-23 | 1
28 | 1Ω |  | R1, R2, R3, R4 | 0603-1 | 4
29 | 2.4Ω |  | R5, R8 | 0805-1 | 2
30 | 12kΩ |  | R6 | 0603-1 | 1
31 | 20kΩ |  | R7 | 0603-1 | 1
32 | 10kΩ |  | R9, R35, R45, R53 | 0603-1 | 4
33 | 4.3kΩ |  | R10 | 0603-1 | 1
34 | 3.3kΩ |  | R11 | 0603-1 | 1
35 | 30kΩ |  | R12 | 0603-1 | 1
36 | 100kΩ |  | R13, R14 | 0603-1 | 2
37 | 3kΩ |  | R15 | 0603-1 | 1
38 | 510Ω |  | R16 | 0603-1 | 1
39 | 68kΩ |  | R17, R55 | 0603-1 | 2
40 | 4mΩ |  | R22, R36 | 2512 | 2
41 | RreciseR_30k |  | R23, R32 | 0603-1 | 2
42 | 7.5kΩ |  | R25, R26, R37, R38, R48, R49, R50, R51 | 0805-1 | 8
43 | RreciseR_3k |  | R27, R34 | 0603-1 | 2
44 | RreciseR_5.1Ω |  | R29, R31, R58, R59, R60, R61 | 0603-1 | 6
45 | 6mΩ |  | R30 | 2512 | 1
46 | NCP18XH103F03RB |  | R33 | 0603-1 | 1
47 | 1.6kΩ |  | R39 | 0603-1 | 1
48 | RreciseR_10k |  | R40 | 0603-1 | 1
49 | RreciseR_31.6k |  | R41 | 0603-1 | 1
50 | 5.1kΩ |  | R42, R43 | 0603-1 | 2
51 | 120Ω |  | R44 | 0603-1 | 1
52 | 100Ω |  | R46, R47 | 0603-1 | 2
53 | 2.4Ω |  | R52 | 0603-1 | 1
54 | 910Ω |  | R54 | 0603-1 | 1
55 | DSHP01TSGET |  | SW1 | SW-SMD_DSHP01TSGET | 1
56 | 1TS002B-2700-5000 |  | SW2 | SW_PB2_A1 | 1
57 | 2EDF7275KXUMA1 |  | U1, U2 | LGA-13 | 2
58 | SY8303A |  | U3, U6 | TSOT23-8 | 2
59 | AMS1117-5.0 |  | U4 | SOT-223 | 1
60 | RT9013-33GB |  | U5 | SOT-23-5_L3.0-W1.7-P0.95-LS2.8-BL | 1
61 | COS722SR |  | U7, U10 | SOIC127P610X175-8N | 2
62 | INA197AIDBVT |  | U8 | SOT-23-5_L3.0-W1.7-P0.95-LS2.8-BL | 1
63 | INA240A1DR |  | U9, U11 | SOIC127P610X175-8N | 2
64 | CJ431_C3113 |  | U12 | SOT-23 | 1
65 | STM32G474CET6 |  | U13 | LQFP-48_M | 1
66 | SN65HVD232DR |  | U14 | SOIC127P610X175-8N | 1
67 | X322525MOB4SI |  | X1 | OSC-3225 | 1
68 | PZ254V-11-07P |  | H1 | OLED_13inch | 1
69 | 15uH |  | L1 | L-SMD-22 | 1

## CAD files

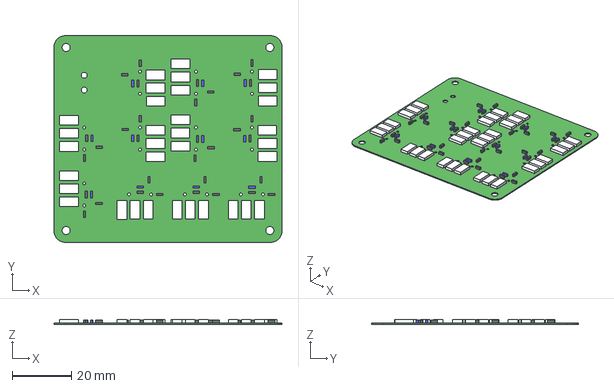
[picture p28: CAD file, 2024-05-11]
CapBank/超级电容组_高能高泄_330.step
77.2 x 70.0 x 1.61 mm

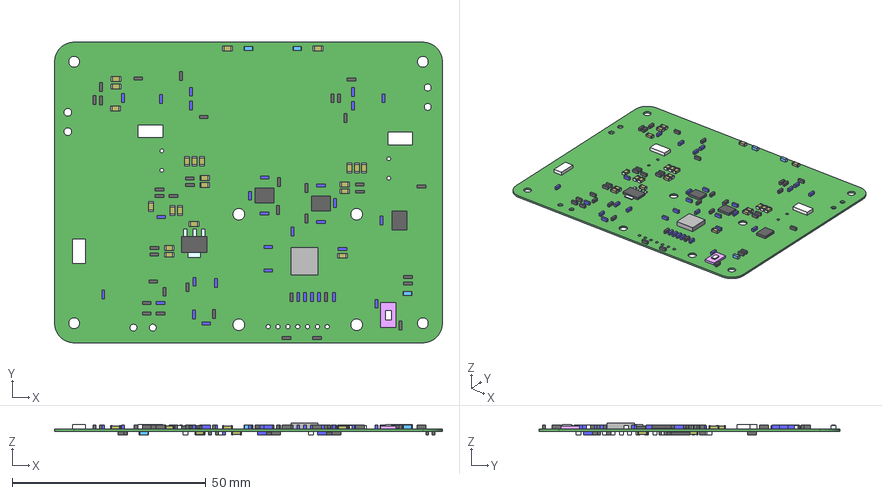
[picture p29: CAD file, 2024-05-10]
Hardware/PCB_Prj/超级电容控制器DEMO5.step
100.1 x 77.6 x 3.22 mm

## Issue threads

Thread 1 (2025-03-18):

无法执行main函数

FIRAgod, 2025-03-18:
我们使用了这版超级电容，但是进行代码烧录后，使用keil调试发现无法执行main函数中的操作，没有运行main函数，在keil调试中变量也没有更新，请问作者有遇到过相似的问题吗

ZhuaX0, 2025-03-18:
晚上好。
你提到的这种情况可能是错误配置了启动项(boot)导致代码不从FLASH开始运行。你可以尝试通过ST-Link Utility或者Cube Prog（可能有用）更改nBOOT1/nBOOT0/nSWBOOT0这三个标志位引导STM32程序从FLASH开始运行。具体改那个我不记得了，你可以参考ST发布的文档RM0440

FIRAgod, 2025-03-21:
无法运行main函数的问题已经解决，非常感谢！但是遇到一个新问题，在运行过程中，我们的电容组电压是1.5v低于3.2V，导致Vcap_Level = Risk;从而一直无法进入work状态，请问是电容组电压需要我们自己设置吗，还是我们在使用过程中存在问题

ZhuaX0, 2025-03-24:
你好
电容控制器对电容组具有欠压保护功能，使用时请确保电容组电压不低于3.5V。在实际比赛中可以购买淘宝的恒流恒压模块对电容组预充电

Closed 2025-05-26.

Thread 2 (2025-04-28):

请问simulink仿真中为什么与电池相连的电阻上面标Ichassis_R而非Ibat，看您手册和代码注释似乎是电池

wfnyyds, 2025-04-28:
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

ZhuaX0, 2025-04-30:
你好。
Simulink中，Ichassis_R的命名方式基于裁判系统命名
代码中指明为电池，基于实际电气拓扑
两者指代实际相同，这里在命名方式有欠考虑

wfnyyds, 2025-04-30:
好的，感谢您的回答

---原始邮件---
发件人: ***@***.***&gt;
发送时间: 2025年4月30日(周三) 下午2:10
收件人: ***@***.***&gt;;
抄送: ***@***.******@***.***&gt;;
主题: Re: [ZhuaX0/RoboMasterSuperCapCtrller_Adernal] 请问simulink仿真中为什么与电池相连的电阻上面标Ichassis_R而非Ibat，看您手册和代码注释似乎是电池 (Issue #2)

 ZhuaX0 left a comment (ZhuaX0/RoboMasterSuperCapCtrller_Adernal#2)

你好。
 Simulink中，Ichassis_R的命名方式基于裁判系统命名
 代码中指明为电池，基于实际电气拓扑
 两者指代实际相同，这里在命名方式有欠考虑

—
Reply to this email directly, view it on GitHub, or unsubscribe.
You are receiving this because you authored the thread.Message ID: ***@***.***&gt;

Closed 2025-05-26.

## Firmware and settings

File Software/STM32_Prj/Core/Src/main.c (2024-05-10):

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
/* Includes ------------------------------------------------------------------*/
#include "main.h"
#include "adc.h"
#include "dma.h"
#include "fdcan.h"
#include "hrtim.h"
#include "spi.h"
#include "tim.h"
#include "usart.h"
#include "gpio.h"

/* USER CODE BEGIN Includes */
#include "iwdg.h"

//Board Supply Package
#include "AnalogSignal.h"
#include "VOFAplus_DataUpload.h"
#include "led.h"

//APP
#include "AlarmSystem.h"
#include "Display.h"
#include "LoopCtrl.h"
#include "Mode.h"
#include "UsrMsg.h"
#include "Safety.h"
/* USER CODE END Includes */


/* USER CODE BEGIN PV */
float Temp = 0.0;//temp
/* USER CODE END PV */

void SystemClock_Config(void);
/**
  * @brief  The application entry point.
  * @retval int
  */
int main(void)
{
  /* MCU Configuration--------------------------------------------------------*/

  /* Reset of all peripherals, Initializes the Flash interface and the Systick. */
  HAL_Init();

  /* Configure the system clock */
  SystemClock_Config();

  /* Initialize all configured peripherals */
  MX_GPIO_Init();
  MX_DMA_Init();
  MX_ADC1_Init();
  MX_ADC2_Init();
  MX_ADC3_Init();
  MX_HRTIM1_Init();
  MX_TIM6_Init();
  MX_USART1_UART_Init();
  MX_FDCAN1_Init();
  MX_SPI1_Init();
  /* USER CODE BEGIN 2 */
	//OLED清屏、初始化、开机界面
	OLED_Clear();
	LED_Init();
	Display_BootUpInterface();
	
	//闹钟系统初始化
	AlarmSystem_Init();
	
	//安全管理初始化
	Safety_Init();

	//模拟信号初始化
	AnalogSignal_AnalogData_Init(15, 32, 64, 15, 64);
	
	//HRTIM&ADC启动
//	HAL_ADCEx_Calibration_Start(&hadc1, ADC_SINGLE_ENDED);
//	HAL_ADCEx_Calibration_Start(&hadc2, ADC_SINGLE_ENDED);
	HAL_ADC_Start_DMA(&hadc1, (uint32_t *)(&AnalogSignal_CapData_RxBuffer[0][0][0]), 96);
	HAL_ADC_Start_DMA(&hadc2, (uint32_t *)(&AnalogSignal_SRCData_RxBuffer[0][0][0]), 64);
	HAL_HRTIM_WaveformCountStart_IT(&hhrtim1, HRTIM_TIMERID_MASTER|HRTIM_TIMERID_TIMER_A|HRTIM_TIMERID_TIMER_B);
	
	//等待填满缓冲&校准模拟信号数据
	uint8_t InitDelay = AlarmSystem_ChannelActive(50, 0);
	while(AlarmSystem_GetBellRing(&InitDelay) == Clocking);
	AnalogSignal_AnalogData_Calibration();
	Safety_INA240cali_ItemCheck(AnalogSignal_FilteredData[Isource], AnalogSignal_FilteredData[Icap]);
	
	//开机界面时间尺度上可视(帅)，等待随逐周期控制的安全检查给出稳定评估结果
	InitDelay = AlarmSystem_ChannelActive(450, 0);
	while(AlarmSystem_GetBellRing(&InitDelay) == Clocking);
	OLED_Clear();
	InitDelay = AlarmSystem_ChannelActive(500, 0);
	Display_LogoInterface();
	while(AlarmSystem_GetBellRing(&InitDelay) == Clocking);
	
	//模式管理初始化
	Mode_Init();
	
	//用户通讯初始化
	UsrMsg_Init();
	
	//OLED清屏、准备界面
	OLED_Clear();
	Display_PrepareInterface();
	Display_Mode_DataUpdateInterface(Silent);
	Display_Exceed_DataUpdateInterface(0x00);
	
	//bxCAN(classic)启动
	MX_FDCAN_Start();
	UsrMsg_StdByFrame_Transmit(&hfdcan1, 0xFF);
	
	//任务时基
	uint8_t TempCheck_NoBlockDelay = AlarmSystem_ChannelActive(10, 1U);
	uint8_t FbFrameTx_NoBlockDelay = AlarmSystem_ChannelActive(500, 1U);
	uint8_t HeartBeatLED_Delay = AlarmSystem_ChannelActive(250, 1U);
	uint8_t OLED_Update_NoBlockDelay = AlarmSystem_ChannelActive(500, 1U);
	
	//看门狗使能
	MX_IWDG_Init();
	
  /* USER CODE END 2 */

  /* Infinite loop */
  /* USER CODE BEGIN WHILE */
  while (1)
  {
		//安全检查
		HAL_IWDG_Refresh(&hiwdg);
		if(AlarmSystem_GetBellRing(&TempCheck_NoBlockDelay) == Ring)
		{
			Safety_Temp_ItemCheck(AnalogSignal_GetTemp());
		}
		
		//决策
		if(UsrMsg_InitData.UpdateTrigger == 1U)//更新电容组类型
		{
			UsrMsg_InitData.UpdateTrigger = 0U;
			
			Mode_CapType_Set(UsrMsg_InitData.CapTypeGet);
		}
		
		if(UsrMsg_CtrlData.Pchassis_UpdateTrigger == 1U)//更新裁判限制功率
		{
			UsrMsg_CtrlData.Pchassis_UpdateTrigger = 0U;
			
			Mode_ExpectPchassis_Set(UsrMsg_CtrlData.PchassisGet_f);
		}
		if(UsrMsg_CtrlData.Exceed_UpdateTrigger == 1U)//更新Exceed开启状态
		{
			UsrMsg_CtrlData.Exceed_UpdateTrigger = 0U;
			
			Mode_Exceed_Set(UsrMsg_CtrlData.ExceedGet);
		}
		if(UsrMsg_CtrlData.Mode_UpdateTrigger == 1U)//更新工作模式
		{
			UsrMsg_CtrlData.Mode_UpdateTrigger = 0U;
			
			switch(UsrMsg_CtrlData.ModeGet)
			{
				case 0x00:
				{
					Mode_Silent();
				}
				break;
				case 0x01:
				{
					Mode_Work();
				}
				break;
				case 0x02:
				{
					Mode_Charge();
				}
				break;
				default:;
			}
		}
		
		//上位机反馈
		if(AlarmSystem_GetBellRing(&FbFrameTx_NoBlockDelay) == Ring)
		{
			float WorkIntensity1 = __ANALOGSIGNAL_DTS_CNVT(AnalogSignal_FilteredData[Icap], Icap) / 10.0f;
			WorkIntensity1 = (WorkIntensity1>=0 ? WorkIntensity1 : (WorkIntensity1*(-1.0f)));
			float WorkIntensity2 = __ANALOGSIGNAL_DTS_CNVT(AnalogSignal_FilteredData[Vbat], Vbat) * __ANALOGSIGNAL_DTS_CNVT(AnalogSignal_FilteredData[Isource], Isource) / 205.0f;
			WorkIntensity2 = (WorkIntensity2>=0 ? WorkIntensity2 : (WorkIntensity2*(-1.0f)));
			
			UsrMsg_FbFrame_Transmit(&hfdcan1, 
															__ANALOGSIGNAL_DTS_CNVT(AnalogSignal_FilteredData[Vcap], Vcap)-__CAP_ESR*__ANALOGSIGNAL_DTS_CNVT(AnalogSignal_FilteredData[Icap], Icap),
															WorkIntensity1,
															WorkIntensity2,
															__ANALOGSIGNAL_DTS_CNVT(AnalogSignal_FilteredData[Vbat], Vbat) * __ANALOGSIGNAL_DTS_CNVT(AnalogSignal_FilteredData[Ichassis], Ichassis));
		}
		
		//心跳灯
		if(AlarmSystem_GetBellRing(&HeartBeatLED_Delay)==Ring)
		{
			HAL_GPIO_TogglePin(LED_RED_GPIO_Port, LED_RED_Pin);
		}
		
		//OLED显示数据更新任务
		if(AlarmSystem_GetBellRing(&OLED_Update_NoBlockDelay)==Ring)
		{
			Display_Vcap_DataUpdateInterface(__ANALOGSIGNAL_DTS_CNVT(AnalogSignal_FilteredData[Vcap], Vcap));
		}
		if(Safety_ItemLevel_ChangeTrigger == 1U)
		{
			Safety_ItemLevel_ChangeTrigger = 0U;
			
			Display_SafetyCode_DataUpdateInterface(Safety_ItemLevel);
			UsrMsg_SafeFrame_Transmit(&hfdcan1, Safety_ItemLevel);
		}
		
    /* USER CODE END WHILE */

    /* USER CODE BEGIN 3 */
  }
  /* USER CODE END 3 */
}

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
/* USER CODE BEGIN 4 */
void HAL_ADC_ErrorCallback(ADC_HandleTypeDef *hadc)
{
	AnalogSignal_ADCDMA_OVRStop(hadc);
	Safety_DMAden_ItemCheck();
}

void HAL_HRTIM_RepetitionEventCallback(HRTIM_HandleTypeDef * hhrtim, uint32_t TimerIdx)
{
	//监测ADC是否发生溢出事件，若溢出重新恢复ADC转换与DMA传输
	//并跳过这REP周期的模拟信号数据处理与HRPWM调制
	uint8_t ADC_OVR_Flag=0;
	if(__HAL_ADC_GET_FLAG(&hadc1, ADC_FLAG_OVR)==1UL)
	{
		AnalogSignal_ADCDMA_OVRRecovery(&hadc1);
		ADC_OVR_Flag=1;
	}
	if(__HAL_ADC_GET_FLAG(&hadc2, ADC_FLAG_OVR)==1UL)
	{
		AnalogSignal_ADCDMA_OVRRecovery(&hadc2);
		ADC_OVR_Flag=1;
	}
	
	//模拟信号处理&环路控制
	if(ADC_OVR_Flag==0)
	{
		AnalogSignal_AnalogData_Update();
		if(AnalogSignal_CaliReady==1U)
		{
			Safety_Voltage_ItemCheck(__ANALOGSIGNAL_DTS_CNVT(AnalogSignal_FilteredData[Vbat], Vbat),
															 __ANALOGSIGNAL_DTS_CNVT(AnalogSignal_FilteredData[Vcap], Vcap));
			Safety_Current_ItemCheck(__ANALOGSIGNAL_DTS_CNVT(AnalogSignal_FilteredData[Isource], Isource),
															 __ANALOGSIGNAL_DTS_CNVT(AnalogSignal_FilteredData[Icap], Icap));
			Safety_deltaP_ItemCheck(__ANALOGSIGNAL_DTS_CNVT(AnalogSignal_FilteredData[Vbat], Vbat),
															__ANALOGSIGNAL_DTS_CNVT(AnalogSignal_FilteredData[Isource], Isource),
															__ANALOGSIGNAL_DTS_CNVT(AnalogSignal_FilteredData[Vcap], Vcap),
															__ANALOGSIGNAL_DTS_CNVT(AnalogSignal_FilteredData[Icap], Icap));
		}
		LoopCtrl_Main(
			__ANALOGSIGNAL_DTS_CNVT(AnalogSignal_FilteredData[Icap], Icap),
			__ANALOGSIGNAL_DTS_CNVT(AnalogSignal_FilteredData[Ichassis], Ichassis),
			__ANALOGSIGNAL_DTS_CNVT(AnalogSignal_FilteredData[Vcap], Vcap),
			__ANALOGSIGNAL_DTS_CNVT(AnalogSignal_FilteredData[Isource], Isource),
			__ANALOGSIGNAL_DTS_CNVT(AnalogSignal_FilteredData[Vbat], Vbat));
	}
	
	//向上位机回传数据
	float AnalogData_Upload[2];
	
//	AnalogData_Upload[0] = __ANALOGSIGNAL_DTS_CNVT(AnalogSignal_RealtimeData[Icap], Icap);
//	AnalogData_Upload[1] = __ANALOGSIGNAL_DTS_CNVT(AnalogSignal_FilteredData[Icap], Icap);
	
	AnalogData_Upload[0] = __ANALOGSIGNAL_DTS_CNVT(AnalogSignal_FilteredData[Vbat], Vbat)*__ANALOGSIGNAL_DTS_CNVT(AnalogSignal_FilteredData[Ichassis], Ichassis);
	AnalogData_Upload[1] = __ANALOGSIGNAL_DTS_CNVT(AnalogSignal_FilteredData[Vcap], Vcap);

	VOFA_DataJustFloat_Upload(AnalogData_Upload, 2);
}

uint8_t RxFifo0NewMsg_InitLock = 0U;
void HAL_FDCAN_RxFifo0Callback(FDCAN_HandleTypeDef *hfdcan, uint32_t RxFifo0ITs)
{
	if(hfdcan==&hfdcan1
	&& RxFifo0ITs==FDCAN_IT_RX_FIFO0_NEW_MESSAGE)
	{
		FDCAN_RxHeaderTypeDef FDCAN_RxHeader;
		uint8_t FDCAN_RxData[8];
		HAL_FDCAN_GetRxMessage(hfdcan, FDCAN_RX_FIFO0, &FDCAN_RxHeader, FDCAN_RxData);
		
		switch(FDCAN_RxHeader.Identifier)
		{
			case UsrMsgRx_CtrlID:
			{
				UsrMsg_CtrlFrame_Unpack(FDCAN_RxData);
			}
			break;
			case UsrMsgRx_InitID:
			{
				if(RxFifo0NewMsg_InitLock == 0U)
				{
					RxFifo0NewMsg_InitLock = 1U;
					UsrMsg_InitFrame_Unpack(FDCAN_RxData);
				}
			}
			break;
			default:;
		}
	}
}

void HAL_FDCAN_ErrorStatusCallback(FDCAN_HandleTypeDef *hfdcan, uint32_t ErrorStatusITs)
{
	Safety_bxCAN_ItemCheck();
}
	
/* USER CODE END 4 */
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


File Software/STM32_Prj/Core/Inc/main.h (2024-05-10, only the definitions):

#define CAP_Vdet_Pin GPIO_PIN_0
#define CAP_Vdet_GPIO_Port GPIOA
#define DCcap_Idet_Pin GPIO_PIN_1
#define DCcap_Idet_GPIO_Port GPIOA
#define BAT_Vdet_Pin GPIO_PIN_4
#define BAT_Vdet_GPIO_Port GPIOA
#define DCsource_Idet_Pin GPIO_PIN_6
#define DCsource_Idet_GPIO_Port GPIOA
#define Chassis_Idet_Pin GPIO_PIN_0
#define Chassis_Idet_GPIO_Port GPIOB
#define TemDet_Pin GPIO_PIN_1
#define TemDet_GPIO_Port GPIOB
#define LED_RED_Pin GPIO_PIN_11
#define LED_RED_GPIO_Port GPIOB
#define LED_BLUE_Pin GPIO_PIN_12
#define LED_BLUE_GPIO_Port GPIOB
#define CapDriver_Enable_Pin GPIO_PIN_15
#define CapDriver_Enable_GPIO_Port GPIOB
#define CapDriver_HighPWM_Pin GPIO_PIN_8
#define CapDriver_HighPWM_GPIO_Port GPIOA
#define CapDriver_LowPWM_Pin GPIO_PIN_9
#define CapDriver_LowPWM_GPIO_Port GPIOA
#define SourceDriver_HighPWM_Pin GPIO_PIN_10
#define SourceDriver_HighPWM_GPIO_Port GPIOA
#define SourceDriver_LowPWM_Pin GPIO_PIN_11
#define SourceDriver_LowPWM_GPIO_Port GPIOA
#define SourceDriver_Enable_Pin GPIO_PIN_12
#define SourceDriver_Enable_GPIO_Port GPIOA
#define OLED_DC_Pin GPIO_PIN_15
#define OLED_DC_GPIO_Port GPIOA
#define OLED_SCK_Pin GPIO_PIN_3
#define OLED_SCK_GPIO_Port GPIOB
#define OLED_RES_Pin GPIO_PIN_4
#define OLED_RES_GPIO_Port GPIOB
#define OLED_MOSI_Pin GPIO_PIN_5
#define OLED_MOSI_GPIO_Port GPIOB
#define CCMRAM __attribute__((section("ccmram")))
#define __CAP_ESR (0.17f)

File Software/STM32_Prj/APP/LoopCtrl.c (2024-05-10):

#include "LoopCtrl.h"
#include "DCDC.h"
#include "AnalogSignal.h"

uint8_t LoopCtrl_GoingFlag=0;

LoopCtrl_KpKiKdInit_Typedef LoopCtrl_KpKiKdStructure;
LoopCtrl_LimitInit_Typedef LoopCtrl_LimitStructure;

LoopCtrl_PID_Typedef LoopCtrl_PID_VcapHigh;
LoopCtrl_PID_Typedef LoopCtrl_PID_VcapLow;
LoopCtrl_PID_Typedef LoopCtrl_PID_Icap;
LoopCtrl_ffPID_Typedef LoopCtrl_ffPID_Psource;
LoopCtrl_PID_Typedef LoopCtrl_PID_Pchassis;

float LoopCtrl_ExpectPchassis,LoopCtrl_ExpectVcapH,LoopCtrl_ExpectVcapL;
float Expect_Icap_Last;

/**
  ************************************************************************** 
  ** @name          : LoopCtrl_Init
  ** @brief         : Initialise the parameters of each control loop.
  ** @param         : void
  ** @retval        : void
  ************************************************************************** 
**/
void LoopCtrl_StructInit(void)
{
	//电流环KpKiKd初始化
	LoopCtrl_KpKiKdStructure.IcapLoop_Kp = 0.0007f;//simulink result:0.0003
	LoopCtrl_KpKiKdStructure.IcapLoop_Ki = 0.00062f;//simulink result:0.001
	LoopCtrl_KpKiKdStructure.IcapLoop_Kd = 0.0f;//simulink result:0.0
	//Psource环KpKiKd初始化
	LoopCtrl_KpKiKdStructure.PsourceLoop_Kp = 0.0f;//simulink result:0.03
	LoopCtrl_KpKiKdStructure.PsourceLoop_Ki = 0.0f;//simulink result:0.01
	LoopCtrl_KpKiKdStructure.PsourceLoop_Kd = 0.0f;//simulink result:0.0
	//电池功率环KpKiKd初始化
	LoopCtrl_KpKiKdStructure.PchassisLoop_Kp = 0.05f;//simulink result:0.7
	LoopCtrl_KpKiKdStructure.PchassisLoop_Ki = 0.008f;//simulink result:0.09
	LoopCtrl_KpKiKdStructure.PchassisLoop_Kd = 0.0f;//simulink result:0.0
	//高限电压环KpKiKd初始化
	LoopCtrl_KpKiKdStructure.VcapHighLoop_Kp = 0.001f;//simulink result:0.001
	LoopCtrl_KpKiKdStructure.VcapHighLoop_Ki = 0.0025f;//simulink result:0.01
	LoopCtrl_KpKiKdStructure.VcapHighLoop_Kd = 0.0f;//simulink result:0.0
	//低限电压环KpKiKd初始化
	LoopCtrl_KpKiKdStructure.VcapLowLoop_Kp = 0.001f;//simulink result:0.001
	LoopCtrl_KpKiKdStructure.VcapLowLoop_Ki = 0.0025f;//simulink result:0.01
	LoopCtrl_KpKiKdStructure.VcapLowLoop_Kd = 0.0f;//simulink result:0.0
	
	//电流环限幅初始化(test only
	LoopCtrl_LimitStructure.Icap_IntegMax  = 28.0f/19.5f;
	LoopCtrl_LimitStructure.Icap_IntegMin  = 3.5f /27.5f;
	LoopCtrl_LimitStructure.Icap_OutputMax = 28.0f/19.5f;
	LoopCtrl_LimitStructure.Icap_OutputMin = 3.5f /27.5f;
	//Psource环限幅初始化(test only
	LoopCtrl_LimitStructure.Psource_PID_IntegMax  = 0.5f;
	LoopCtrl_LimitStructure.Psource_PID_IntegMin  = -0.5f;
	LoopCtrl_LimitStructure.Psource_PID_OutputMax = 0.5f;
	LoopCtrl_LimitStructure.Psource_PID_OutputMin = -0.5f;
	LoopCtrl_LimitStructure.Psource_ffPID_OutputMax = 10.0f;
	LoopCtrl_LimitStructure.Psource_ffPID_OutputMin = -10.0f;
	//Pchassis环限幅初始化(test only
	LoopCtrl_LimitStructure.Pchassis_IntegMin  = -205.0f;
	LoopCtrl_LimitStructure.Pchassis_OutputMin = -205.0f;
	//高限电压环限幅初始化(test only
	LoopCtrl_LimitStructure.VcapHigh_IntegMax  = 28.0f/19.5f;
	LoopCtrl_LimitStructure.VcapHigh_IntegMin  = 28.0f/27.5f;
	LoopCtrl_LimitStructure.VcapHigh_OutputMax = 28.0f/19.5f;
	LoopCtrl_LimitStructure.VcapHigh_OutputMin = 28.0f/27.5f;
	//低限电压环限幅初始化(test only
	LoopCtrl_LimitStructure.VcapLow_IntegMax  = 3.5f/19.5f;
	LoopCtrl_LimitStructure.VcapLow_IntegMin  = 3.5f/27.5f;
	LoopCtrl_LimitStructure.VcapLow_OutputMax = 3.5f/19.5f;
	LoopCtrl_LimitStructure.VcapLow_OutputMin = 3.5f/27.5f;
}

/**
  ************************************************************************** 
  ** @name          : LoopCtrl_Start
  ** @brief         : Perform the necessary parameter preprocessing to start the loop calculation with the output HRPWM.
  ** @param         : void
  ** @retval        : HAL_StatusTypeDef,if HAL_OK,loop start successful.if HAL_ERROR,Refuse due to security concerns.
  ************************************************************************** 
**/
HAL_StatusTypeDef LoopCtrl_Start(LoopCtrl_KpKiKdInit_Typedef *LoopCtrl_KpKiKdInit, LoopCtrl_LimitInit_Typedef *LoopCtrl_LimitInit,
																									float ExpectChassis, float ExpectVcapH, float ExpectVcapL)
{
	HAL_GPIO_WritePin(LED_BLUE_GPIO_Port, LED_BLUE_Pin, GPIO_PIN_RESET);
	
	//电容电流环KpKiKd
	LoopCtrl_PID_Icap.ArmPID_Instance.Kp = LoopCtrl_KpKiKdInit->IcapLoop_Kp;
	LoopCtrl_PID_Icap.ArmPID_Instance.Ki = LoopCtrl_KpKiKdInit->IcapLoop_Ki;
	LoopCtrl_PID_Icap.ArmPID_Instance.Kd = LoopCtrl_KpKiKdInit->IcapLoop_Kd;
	//Psource环KpKiKd
	LoopCtrl_ffPID_Psource.PID_Instance.ArmPID_Instance.Kp = LoopCtrl_KpKiKdInit->PsourceLoop_Kp;
	LoopCtrl_ffPID_Psource.PID_Instance.ArmPID_Instance.Ki = LoopCtrl_KpKiKdInit->PsourceLoop_Ki;
	LoopCtrl_ffPID_Psource.PID_Instance.ArmPID_Instance.Kd = LoopCtrl_KpKiKdInit->PsourceLoop_Kd;
	//Pchassis环KpKiKd
	LoopCtrl_PID_Pchassis.ArmPID_Instance.Kp = LoopCtrl_KpKiKdInit->PchassisLoop_Kp;
	LoopCtrl_PID_Pchassis.ArmPID_Instance.Ki = LoopCtrl_KpKiKdInit->PchassisLoop_Ki;
	LoopCtrl_PID_Pchassis.ArmPID_Instance.Kd = LoopCtrl_KpKiKdInit->PchassisLoop_Kd;
	//高限电压环KpKiKd
	LoopCtrl_PID_VcapHigh.ArmPID_Instance.Kp = LoopCtrl_KpKiKdInit->VcapHighLoop_Kp;
	LoopCtrl_PID_VcapHigh.ArmPID_Instance.Ki = LoopCtrl_KpKiKdInit->VcapHighLoop_Ki;
	LoopCtrl_PID_VcapHigh.ArmPID_Instance.Kd = LoopCtrl_KpKiKdInit->VcapHighLoop_Kd;
	//低限制电压环KpKiKd
	LoopCtrl_PID_VcapLow.ArmPID_Instance.Kp = LoopCtrl_KpKiKdInit->VcapLowLoop_Kp;
	LoopCtrl_PID_VcapLow.ArmPID_Instance.Ki = LoopCtrl_KpKiKdInit->VcapLowLoop_Ki;
	LoopCtrl_PID_VcapLow.ArmPID_Instance.Kd = LoopCtrl_KpKiKdInit->VcapLowLoop_Kd;
	
	//电容电流环限幅
	LoopCtrl_PID_Icap.IntegMax  = LoopCtrl_LimitInit->Icap_IntegMax;
	LoopCtrl_PID_Icap.IntegMin  = LoopCtrl_LimitInit->Icap_IntegMin;
	LoopCtrl_PID_Icap.OutputMax = LoopCtrl_LimitInit->Icap_OutputMax;
	LoopCtrl_PID_Icap.OutputMin = LoopCtrl_LimitInit->Icap_OutputMin;
	//Psource环限幅
	LoopCtrl_ffPID_Psource.PID_Instance.IntegMax  = LoopCtrl_LimitInit->Psource_PID_IntegMax;
	LoopCtrl_ffPID_Psource.PID_Instance.IntegMin  = LoopCtrl_LimitInit->Psource_PID_IntegMin;
	LoopCtrl_ffPID_Psource.PID_Instance.OutputMax = LoopCtrl_LimitInit->Psource_PID_OutputMax;
	LoopCtrl_ffPID_Psource.PID_Instance.OutputMin = LoopCtrl_LimitInit->Psource_PID_OutputMin;
	LoopCtrl_ffPID_Psource.OutputMax = LoopCtrl_LimitInit->Psource_ffPID_OutputMax;
	LoopCtrl_ffPID_Psource.OutputMin = LoopCtrl_LimitInit->Psource_ffPID_OutputMin;
	//Pchassis环限幅
	LoopCtrl_ExpectPchassisSet(ExpectChassis);
	LoopCtrl_PID_Pchassis.IntegMin  = LoopCtrl_LimitInit->Pchassis_IntegMin;
	LoopCtrl_PID_Pchassis.OutputMin = LoopCtrl_LimitInit->Pchassis_OutputMin;
	//高限电压限幅
	LoopCtrl_PID_VcapHigh.IntegMax  = LoopCtrl_LimitInit->VcapHigh_IntegMax;
	LoopCtrl_PID_VcapHigh.IntegMin  = LoopCtrl_LimitInit->VcapHigh_IntegMin;
	LoopCtrl_PID_VcapHigh.OutputMax = LoopCtrl_LimitInit->VcapHigh_OutputMax;
	LoopCtrl_PID_VcapHigh.OutputMin = LoopCtrl_LimitInit->VcapHigh_OutputMin;
	//低限电压环限幅
	LoopCtrl_PID_VcapLow.IntegMax  = LoopCtrl_LimitInit->VcapLow_IntegMax;
	LoopCtrl_PID_VcapLow.IntegMin  = LoopCtrl_LimitInit->VcapLow_IntegMin;
	LoopCtrl_PID_VcapLow.OutputMax = LoopCtrl_LimitInit->VcapLow_OutputMax;
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

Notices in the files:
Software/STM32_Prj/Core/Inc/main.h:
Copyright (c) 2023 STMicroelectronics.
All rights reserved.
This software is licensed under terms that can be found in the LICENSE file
